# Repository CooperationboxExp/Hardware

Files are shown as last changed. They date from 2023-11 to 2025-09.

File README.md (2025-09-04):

# Hardware

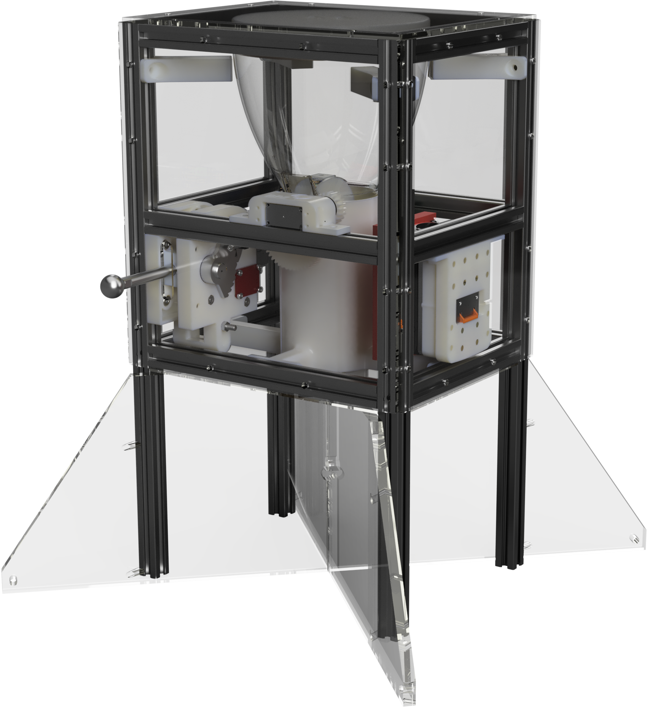
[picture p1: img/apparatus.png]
apparatus


## Publication

Repository: Zenodo  
Publication date: 2024-11-18  



## Electrical wireing

apparatus

## Manufacturing

The files for manufacturing can be found in the following folders:

+ STL/: Contains the STL files for 3D printing the parts.
+ Panels/: Contains the files for cutting the panels.
+ PDF/: Contains the files with specifications, turning and assembly instructions.

Alternatively, you can export all parts from the provided full assemblies with either the `ApparatusAssembly.step` or `ApparatusAssembly.f3z` files.

## BOM

From `BOM.xlsx`:

| Category | Quantity  One apparatus | Quantity four apparatuses | Wear and tear | Amount to order | Type / Length mm | Component | Supplier | URL | Price @ URL | Price for one apparatus. | Price for two apparatus. | Price waer and tear | Price total | Comment |
| --- | --- | --- | --- | --- | --- | --- | --- | --- | --- | --- | --- | --- | --- | --- |
| Housing | 100 | 400 | 0 | 400 | M5 | Nutenstein mit Steg I-Typ Nut 5 [M5] | Motedis | https://www.motedis.com/shop/Nutprofil-Zubehoer/Zubehoer-20-I-Typ-Nut-5/Nutensteine-passend-fuer-Nut-5-I-Typ/Nutenstein-mit-Steg-I-Typ-Nut-5-M5::4226.html | 0,18 € | 18,16 € | 72,64 € | 0,00 € | 72,64 € | |
| Housing | 4 | 16 | 0 | 16 | 500mm | Aluprofil 20x20 I-Typ Nut 5 | Motedis | https://www.motedis.com/shop/Aluprofile/20-I-Typ-Nut-5/Aluprofil-20x20-I-Typ-Nut-5::1076.html | 2,96 € | 11,82 € | 47,28 € | 0,00 € | 47,28 € | |
| Housing | 8 | 32 | 2 | 34 | 180mm, machining M5 L/R | Aluprofil 20x20 I-Typ Nut 5 | Motedis | https://www.motedis.com/shop/Aluprofile/20-I-Typ-Nut-5/Aluprofil-20x20-I-Typ-Nut-5::1076.html | 2,90 € | 23,20 € | 92,80 € | 5,80 € | 98,60 € | |
| Housing | 8 | 32 | 2 | 34 | 240mm, machining M5 L/R | Aluprofil 20x20 I-Typ Nut 5 | Motedis | https://www.motedis.com/shop/Aluprofile/20-I-Typ-Nut-5/Aluprofil-20x20-I-Typ-Nut-5::1076.html | 3,17 € | 25,32 € | 101,28 € | 6,33 € | 107,61 € | |
| Housing | 16 | 64 | 4 | 68 | 20x20 mm | Stahlwinkel 20 verzinkt | Motedis | https://www.motedis.com/shop/Test2-Systematic/Gabelkoepfe-Gabelgelenke/Stahlwinkel-20-verzinkt::9014.html | 0,72 € | 11,52 € | 46,08 € | 2,88 € | 48,96 € | |
| Housing | 56 | 224 | 15 | 239 | M5x6 | Schraube DIN EN ISO 7380 - Linsenkopfschraube | Motedis | https://www.motedis.com/shop/Mechanik-Basiselemente/DIN-Schrauben/Schraube-DIN-EN-ISO-7380-Linsenkopfschraube::1070.html | 0,15 € | 8,42 € | 33,69 € | 2,26 € | 35,95 € | |
| Housing | 56 | 224 | 15 | 239 | M5x8 | Schraube DIN EN ISO 7380 - Linsenkopfschraube | Motedis | https://www.motedis.com/shop/Mechanik-Basiselemente/DIN-Schrauben/Schraube-DIN-EN-ISO-7380-Linsenkopfschraube::1070.html | 0,15 € | 8,42 € | 33,69 € | 2,26 € | 35,95 € | |
| Housing | 56 | 224 | 15 | 239 | M5x10 | Schraube DIN EN ISO 7380 - Linsenkopfschraube | Motedis | https://www.motedis.com/shop/Mechanik-Basiselemente/DIN-Schrauben/Schraube-DIN-EN-ISO-7380-Linsenkopfschraube::1070.html | 0,15 € | 8,42 € | 33,69 € | 2,26 € | 35,95 € | |
| Housing | 56 | 224 | 15 | 239 | M5x12 | Schraube DIN EN ISO 7380 - Linsenkopfschraube | Motedis | https://www.motedis.com/shop/Mechanik-Basiselemente/DIN-Schrauben/Schraube-DIN-EN-ISO-7380-Linsenkopfschraube::1070.html | 0,15 € | 8,42 € | 33,69 € | 2,26 € | 35,95 € | |
| Housing | 0 | 0 | 0 | 0 | M5x12 | Befestigungsschraube DIN 7380 M5x12 vz für Standardverbinder Nut 5 I-Typ | Motedis | https://www.motedis.com/shop/Nutprofil-Zubehoer/Zubehoer-20-I-Typ-Nut-5/Verbinder-Winkel/Befestigungsschraube-DIN-7380-M5x12-vz-f%FCr-Standardverbinder-Nut-5-I-Typ::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 | 0,11 € | 0,00 € | 0,00 € | 0,00 € | 0,00 € | |
| Housing | 20 | 80 | 15 | 95 | M5x16 | Schraube DIN EN ISO 7380 - Linsenkopfschraube | Motedis | https://www.motedis.com/shop/Mechanik-Basiselemente/DIN-Schrauben/Schraube-DIN-EN-ISO-7380-Linsenkopfschraube::1070.html | 0,15 € | 3,01 € | 12,03 € | 2,26 € | 14,29 € | |
| Housing | 0 | 0 | 0 | 0 | 35x220mm | DIN 35 – Hutschiene | Digikey | https://www.digikey.de/product-detail/de/banner-engineering-corporation/DIN-35-220/2170-DIN-35-220-ND/12417670 | 18,25 € | 0,00 € | 0,00 € | 0,00 € | 0,00 € | |
| Housing | 10 | 40 | 15 | 55 | M5x35 | Schraube DIN EN ISO 7380 - Linsenkopfschraube | Motedis | https://www.motedis.com/shop/Mechanik-Basiselemente/DIN-Schrauben/Schraube-DIN-EN-ISO-7380-Linsenkopfschraube::1070.html | 0,39 € | 3,90 € | 15,58 € | 5,84 € | 21,43 € | |
| | | | | | | | | | | | | | | |
| Food Dispenser | 1 | 3 | 0 | 3 | 320x220x3 | Cereal Dispenser | Amazon | https://www.amazon.de/-/en/United-Entertainment-Dispenser-Cornflakes-Cereals/dp/B06XQLSSG6?psc=1 | 29,00 € | 29,00 € | 87,00 € | 0,00 € | 87,00 € | |
| Food Dispenser | 1 | 4 | 0 | 4 | 320x220x3 | Cereal Dispenser | Kaufland | https://www.kaufland.de/product/358105876/?vid=347560386 | 19,90 € | 19,90 € | 79,60 € | 0,00 € | 79,60 € | |
| Food Dispenser | 1 | 4 | 4 | 8 | 900-00008 | Servo Continuous | Digikey | https://www.digikey.de/product-detail/de/parallax-inc/900-00008/900-00008-ND/1774454 | 10,95 € | 10,95 € | 43,80 € | 43,80 € | 87,60 € | |
| | | | | | | | | | | | | | | |
| Lever and lock | 2 | 8 | 4 | 12 | ROB-11965 | Servo 180° | Digikey | https://www.digikey.de/product-detail/en/sparkfun-electronics/ROB-11965/1568-1319-ND/5766906 | 10,95 € | 21,90 € | 87,60 € | 43,80 € | 131,40 € | |
| Lever and lock | 2 | 8 | 1 | 9 | Gleitlager | Igus Gleitlager mit Bund GFM-1618-09 | Motedis | https://www.motedis.com/shop/Dynamik-Basiselemente/Gleitlager/Igus-Gleitlager-mit-Bund-GFM-1618-09::5078.html | 2,44 € | 4,89 € | 19,54 € | 2,44 € | 21,99 € | |
| Lever and lock | 1 | 4 | 0 | 4 | CNC | Lever metal assembly | Internal workshop | | 0,00 € | 0,00 € | 0,00 € | 0,00 € | 0,00 € | |
| Lever and lock | 2 | 8 | 1 | 9 | AD 4, ID 3.54, Hf 16, H1 8.86 4.57 | Druckfeder C105 | Misumi | https://de.misumi-ec.com/vona2/detail/221000016945/?HissuCode=C105&PNSearch=C105 | 0,60 € | 1,20 € | 4,80 € | 0,60 € | 5,40 € | |
| Lever and lock | 1 | 1 | 0 | 1 | | 10279 Zugfeder Inhalt 350 Teile | Conrad | https://www.conrad.de/de/p/10279-zugfeder-inhalt-350-teile-887655.html?refresh=true | 138,65 € | 138,65 € | 138,65 € | 0,00 € | 138,65 € | We ended up using Z 104 41,4x6x0,55 mm |
| Lever and lock | 4 | 16 | 1 | 17 | M5x45 | Zylinderschraube mit Innensechskant nach DIN 912 | Misumi | https://de.misumi-ec.com/vona2/detail/221006347487/?HissuCode=912A2545 | 0,75 € | 3,00 € | 12,00 € | 0,75 € | 12,75 € | |
| Lever and lock | 6 | 24 | 8 | 32 | M5 | Mutter DIN 934 | Motedis | https://www.motedis.com/shop/Mechanik-Basiselemente/Basic-Basics/DIN-Normteile/DIN-Mutter/Mutter-DIN-934::1768.html | 0,29 € | 1,77 € | 7,08 € | 2,36 € | 9,43 € | |
| Lever and lock | 3 | 12 | 0 | 12 | M5x16 | Senkschraube mit Innensechskant nach DIN 7991 | Motedis | https://www.motedis.com/shop/Mechanik-Basiselemente/DIN-Schrauben/Senkschraube-mit-Innensechskant-nach-DIN-7991::1120.html | 0,39 € | 1,17 € | 4,68 € | 0,00 € | 4,68 € | |
| Lever and lock | 1 | 4 | 0 | 4 | M3 | Gewindestange >60mm | Conrad | https://www.conrad.de/de/p/reely-10589-gewindestange-m3-500-mm-stahl-1-st-237094.html | 1,42 € | 1,42 € | 5,68 € | 0,00 € | 5,68 € | |
| Lever and lock | 1 | 4 | 0 | 4 | M5 | Gewindestange >60mm | Conrad | https://www.conrad.de/de/p/reely-10591-m5-gewindestange-m5-500-mm-stahl-1-st-237116.html | 1,92 € | 1,92 € | 7,68 € | 0,00 € | 7,68 € | |
| Lever and lock | 2 | 8 | 2 | 10 | Microswitch | Omron Electronics Inc-EMC Div D2F-5L | Digikey | https://www.digikey.de/product-detail/de/omron-electronics-inc-emc-div/D2F-5L/Z8846-ND/8593137 | 3,19 € | 6,38 € | 25,52 € | 6,38 € | 31,90 € | |
| | | | | | | | | | | | | | | |
| Panels | 1 | 4 | 0 | 4 | 4mm (32,00 €/m²), 1500x700mm | MAKROLON, POLYCARBONAT | Ebay | https://www.ebay.de/itm/263920803844 | 57,75 € | 57,75 € | 231,00 € | 0,00 € | 231,00 € | Alternative to internal workshop |
| Panels | 1 | 4 | 0 | 4 | 10mm (32,00 €/m²), 1500x700mm | MAKROLON, POLYCARBONAT | Ebay | https://www.ebay.de/itm/263920803844 | 136,50 € | 136,50 € | 546,00 € | 0,00 € | 546,00 € | Alternative to internal workshop |
| Panels | 1 | 4 | 0 | 4 | 4mm (32,00 €/m²), 1500x700mm | MAKROLON, POLYCARBONAT | Internal workshop | | 0,00 € | 0,00 € | 0,00 € | 0,00 € | 0,00 € | |
| Panels | 1 | 4 | 0 | 4 | 10mm (32,00 €/m²), 1500x700mm | MAKROLON, POLYCARBONAT | Internal workshop | | 0,00 € | 0,00 € | 0,00 € | 0,00 € | 0,00 € | |
| Panels | 1 | 4 | 0 | 4 | Top.dxf | 4mm Polycarbonat clear | kunststoffplattenonline.de | https://kunststoffplattenonline.de/product/polycarbonat-platten-transparent-klar-4-mm/ | 13,48 € | 13,48 € | 53,92 € | 0,00 € | 53,92 € | Alternative to internal workshop |
| Panels | 2 | 8 | 0 | 8 | Sides.dxf | 4mm Polycarbonat clear | kunststoffplattenonline.de | https://kunststoffplattenonline.de | 14,67 € | 29,34 € | 117,36 € | 0,00 € | 117,36 € | Alternative to internal workshop |
| Panels | 1 | 4 | 0 | 4 | Front.dxf | 4mm Polycarbonat clear | kunststoffplattenonline.de | https://kunststoffplattenonline.de | 17,81 € | 17,81 € | 71,24 € | 0,00 € | 71,24 € | Alternative to internal workshop |
| Panels | 1 | 4 | 0 | 4 | BackPlate.dxf | 4mm Polycarbonat clear | kunststoffplattenonline.de | https://kunststoffplattenonline.de | 16,91 € | 16,91 € | 67,64 € | 0,00 € | 67,64 € | Alternative to internal workshop |
| Panels | 1 | 4 | 0 | 4 | DividerA.dxf | 10mm Polycarbonat clear | kunststoffplattenonline.de | https://kunststoffplattenonline.de/product/polycarbonat-platten-transparent-klar-10-mm/ | 54,17 € | 54,17 € | 216,68 € | 0,00 € | 216,68 € | Alternative to internal workshop |
| Panels | 1 | 4 | 0 | 4 | DividerB.dxf | 10mm Polycarbonat clear | kunststoffplattenonline.de | https://kunststoffplattenonline.de/product/polycarbonat-platten-transparent-klar-10-mm/ | 54,79 € | 54,79 € | 219,16 € | 0,00 € | 219,16 € | Alternative to internal workshop |
| | | | | | | | | | | | | | | |
| Miscellaneous | 5 | 20 | 0 | 20 | 3D Druck ABS+ | ESUN ABS+ 1,75mm nature | vonwange | https://vonwange.com/product/abs-175mm-nature/ | 18,99 € | 94,95 € | 379,80 € | 0,00 € | 379,80 € | |
| Miscellaneous | 1 | 1 | 0 | 1 | 3D Druck Gewindeeinsätze | ruthex Threaded Insert, Brass Threaded Bushings | Amazon | https://www.amazon.de/-/en/ruthex%C2%AE-threaded-Press-fit-plastic-ultrasound/dp/B08K1BVGN9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 | 29,99 € | 29,99 € | 29,99 € | 0,00 € | 29,99 € | |
| | | | | | | | | | | | | | | |
| Battery | 0 | 0 | 0 | 0 | | Bosch Charger | Amazon | https://www.amazon.de/-/en/Bosch-Professional-system-battery-5-0Ah/dp/B00IKI352E | 44,95 € | 0,00 € | 0,00 € | 0,00 € | 0,00 € | Alternative to Bosch Batterie Set |
| Battery | 1 | 4 | 0 | 4 | | Bosch Batterie | Amazon | https://www.amazon.de/-/en/Bosch-Professional-system-battery-5-0Ah/dp/B00IKI352E | 60,00 € | 60,00 € | 240,00 € | 0,00 € | 240,00 € | Alternative to Bosch Batterie Set |
| Battery | 2 | 2 | 0 | 2 | | Bosch Batterie Set | Conrad | https://www.conrad.de/de/p/bosch-professional-1600a01ba3-werkzeug-akku-und-ladegeraet-18-v-li-ion-2127378.html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 | 159,66 € | 319,32 € | 319,32 € | 0,00 € | 319,32 € | |
| Battery | 1 | 4 | 1 | 5 | modified as battery interface | Bosch Adapter | Amazon | https://www.amazon.de/-/en/Ladieshow-Battery-Adaptor-Convert-Converter/dp/B08QJK9DW4/261-3484322-5351609?psc=1 | 22,99 | 22,99 € | 91,96 € | 22,99 € | 114,95 € | |
| | | | | | | | | | | | | | | |
| Controller and electronics | 1 | 4 | 4 | 8 | Control unit expansion board | Whadda Erweiterungsmodul | Conrad | https://www.conrad.de/de/p/whadda-erweiterungsmodul-2481837.html | 9,24 € | 9,24 € | 36,96 € | 36,96 € | 73,92 € | |
| Controller and electronics | 2 | 8 | 4 | 12 | Voltage supply | Joy-it XL6019 Step-up Converter 1 St. | Conrad | https://www.conrad.de/de/p/joy-it-xl6019-step-up-converter-1-st-1697651.html | 4,61 € | 9,22 € | 36,88 € | 18,44 € | 55,32 € | |
| Controller and electronics | 2 | 8 | 2 | 10 | Voltage supply | Pololu Adjustable 4-12V Step-Up Step-Down Spannungsregler S18V20ALV | Conrad | https://www.conrad.de/de/p/pololu-adjustable-4-12v-step-up-step-down-spannungsregler-s18v20alv-802236410.html | 49,54 € | 99,08 € | 396,32 € | 99,08 € | 495,40 € | |
| Controller and electronics | 1 | 4 | 1 | 5 | Control unit | Arduino Board Nano Core, Nano ATMega328 | Conrad | https://www.conrad.de/de/p/arduino-board-nano-core-nano-atmega328-1172623.html | 21,00 € | 21,00 € | 84,00 € | 21,00 € | 105,00 € | |
| Controller and electronics | 1 | 4 | 1 | 5 | Remote control | H-Tronic HT1S Funksender 1-Kanal Frequenz 868.35 MHz 3 V Reichweite max. (im Freifeld) 150 m | Conrad | https://www.conrad.de/de/p/h-tronic-ht1s-funksender-1-kanal-frequenz-868-35-mhz-3-v-reichweite-max-im-freifeld-150-m-1597514.html | 22,68 € | 22,68 € | 90,72 € | 22,68 € | 113,40 € | |
| Controller and electronics | 1 | 4 | 1 | 5 | Remote receiver | H-Tronic HT1E Funkempfänger 1-Kanal Frequenz 868.35 MHz 12 V/DC | Conrad | https://www.conrad.de/de/p/h-tronic-ht1e-funkempfaenger-1-kanal-frequenz-868-35-mhz-12-v-dc-1406364.html | 37,81 € | 37,81 € | 151,24 € | 37,81 € | 189,05 € | |
| Controller and electronics | 1 | 4 | 1 | 5 | Arduino transceiver | WRL-00691 - SPARKFUN TRANSCEIVER BREAKOUT BOARD | Digikey | https://www.digikey.de/de/products/detail/sparkfun-electronics/WRL-00691/5762445 | 21,15 € | 21,15 € | 84,60 € | 21,15 € | 105,75 € | |
| Controller and electronics | 1 | 1 | 0 | 1 | Cabels Battery | eg. Litze 2.5 mm^2 | | | | 0,00 € | 0,00 € | 0,00 € | 0,00 € | Workshop supplies |
| Controller and electronics | 1 | 1 | 0 | 1 | Cabels | eg. Litze 0.25 mm^2 | | | | 0,00 € | 0,00 € | 0,00 € | 0,00 € | Workshop supplies |
| Controller and electronics | 1 | 1 | 0 | 1 | Dupont Connector 2.54mm Pitch | For "pin-header" | | | | 0,00 € | 0,00 € | 0,00 € | 0,00 € | Workshop supplies |
| Controller and electronics | 1 | 1 | 0 | 1 | WAGO Sortiment | | Conrad | https://www.conrad.de/de/p/wago-wa-741-644-verbindungsklemmen-sortiment-flexibel-0-14-4-mm-starr-0-2-4-mm-105-st-1398220.html | 52,09 € | 52,09 € | 52,09 € | 0,00 € | 52,09 € | Workshop supplies |
| Controller and electronics | 1 | 1 | 0 | 1 | Cabels | | | | | 0,00 € | 0,00 € | 0,00 € | 0,00 € | Workshop supplies |
| | | | | | | | | | | | | | | |

## Included CAD

For convenience some files included in this design where imported from external sources.

| Name | Author | Link |
| --- | --- | --- |
| Arduino Nano R3 ATmega 328P | MRMS - WORKSHOP | <https://grabcad.com/library/arduino-nano-r3-atmega-328p-1> |
| DFR0012 pour Arduino Nano | RedOhm | <https://grabcad.com/library/dfr0012-pour-arduino-nano-1> |
| Дрели - шуруповёрт / Drills - screwdriver | Alex Petuhov | <https://grabcad.com/library/drills-screwdriver-1> |
| Battery adapter | bujh bdfyjd | <https://grabcad.com/library/battery-adapter-1> |
| Servo | Amazon Seller | An Amazon page of a similar product that is unfortunately no longer available |

### GrabCAD terms

[https://grabcad.com/terms](https://grabcad.com/terms)

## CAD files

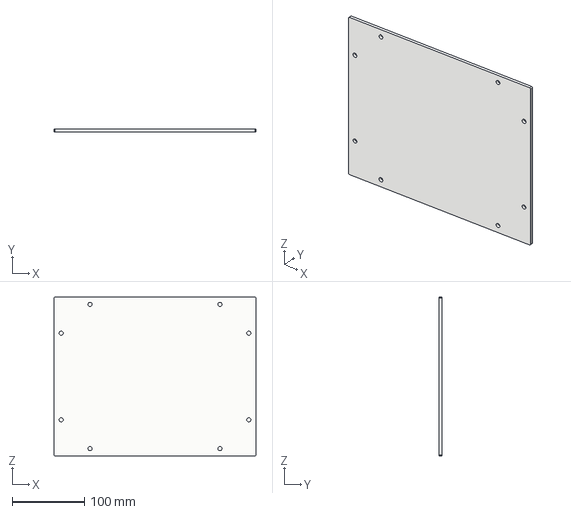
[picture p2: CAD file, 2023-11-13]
Panels/Top.step
280.0 x 4.00 x 220.0 mm

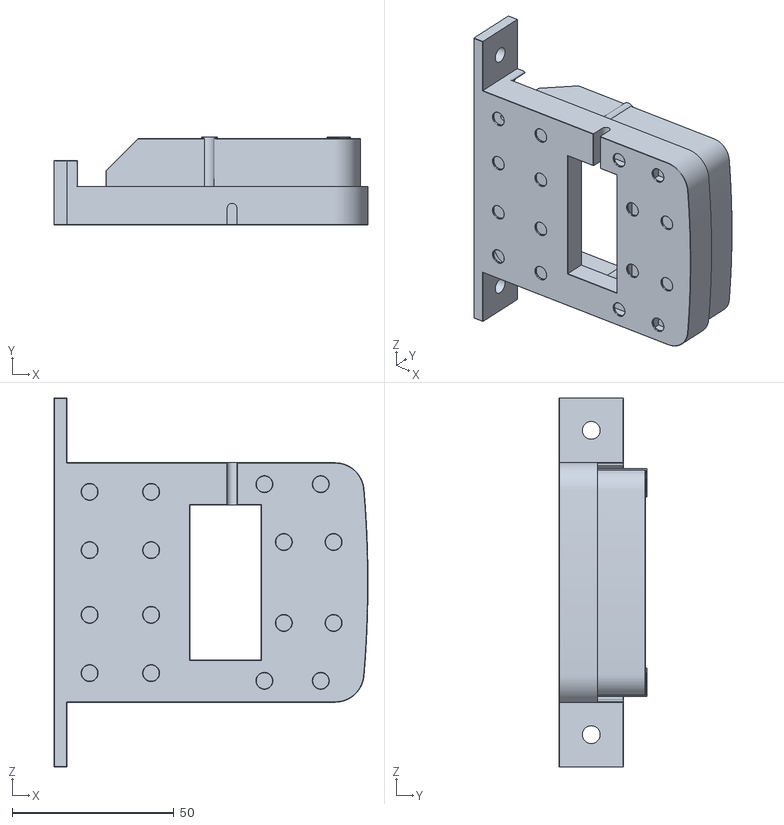
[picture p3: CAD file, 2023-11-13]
STL/BatterySocket_Interface v7.stl
97.0 x 27.2 x 114.0

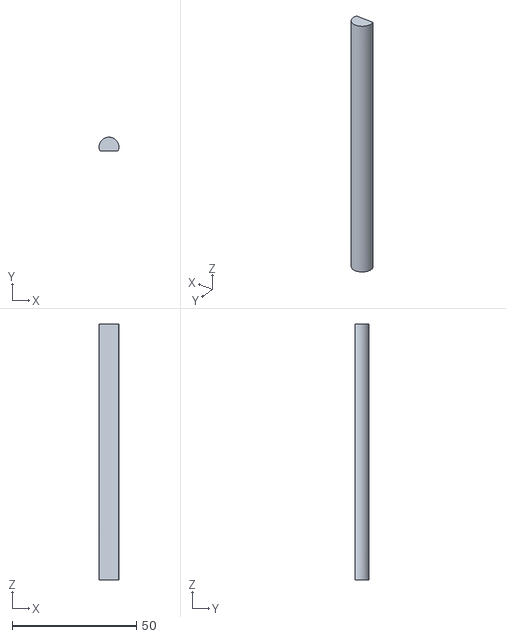
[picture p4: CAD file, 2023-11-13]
STL/Container/Axis.stl
8.00 x 5.50 x 103.0

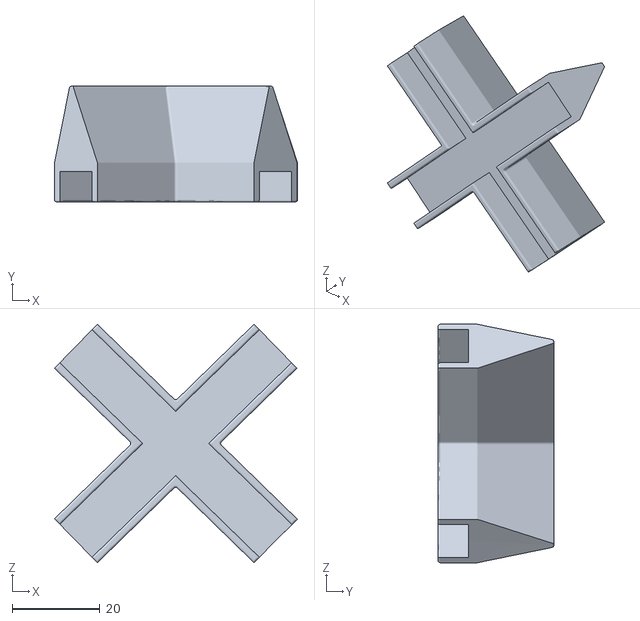
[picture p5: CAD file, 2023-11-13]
STL/Divider/FourSide_DividerModule.stl
55.4 x 26.5 x 54.4

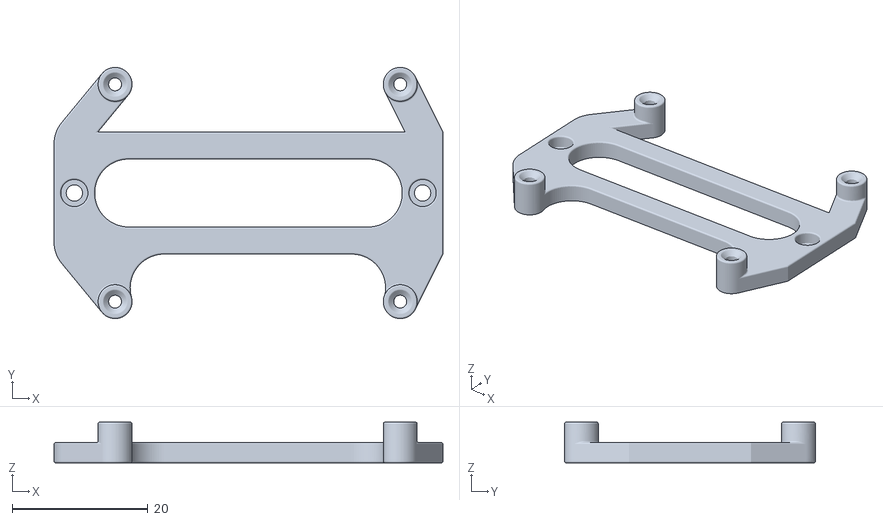
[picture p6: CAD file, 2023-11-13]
STL/Electronics/HT1E_Bracket.stl
57.3 x 37.0 x 6.00

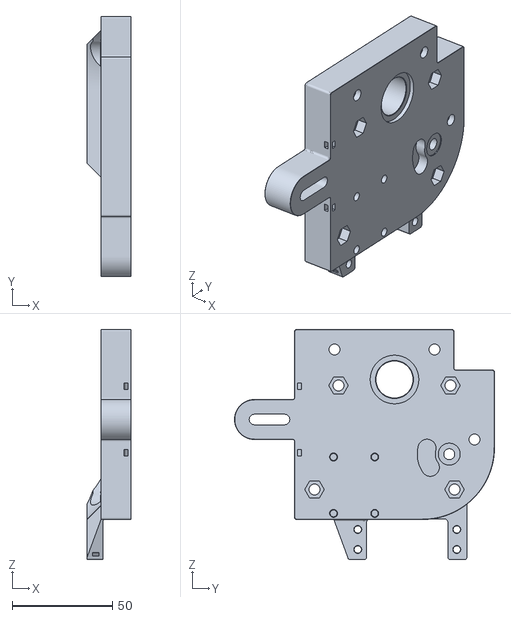
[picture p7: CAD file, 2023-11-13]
STL/Hebel_Assembly v4/Hebel_Plate_R.stl
22.0 x 130.0 x 115.0

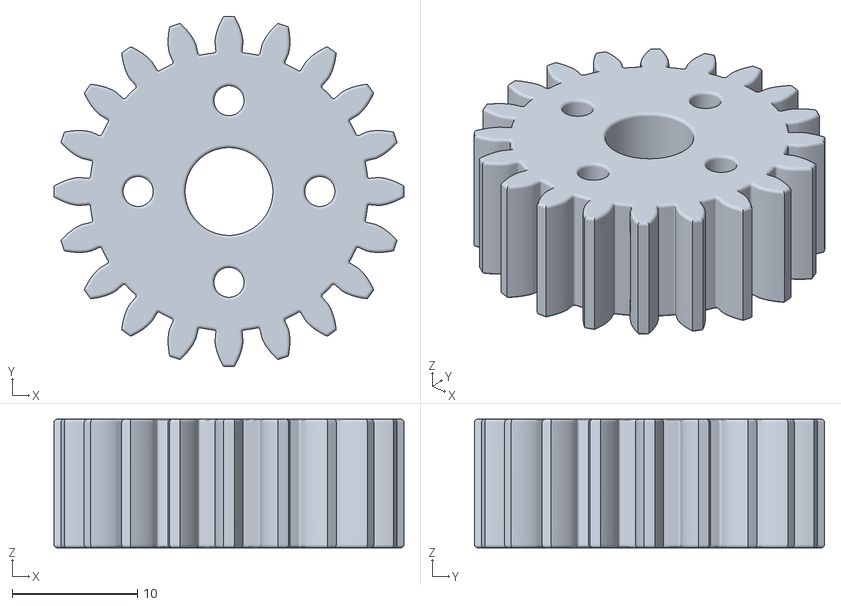
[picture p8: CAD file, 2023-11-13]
STL/ServoGear/GearCore.stl
27.9 x 27.9 x 10.3

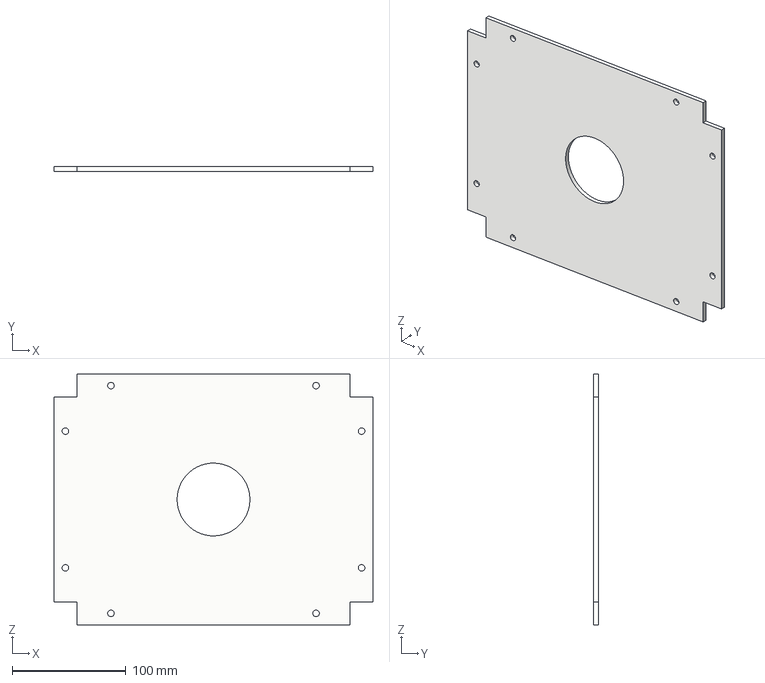
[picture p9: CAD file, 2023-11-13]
Panels/Bottom.step
280.0 x 4.00 x 220.0 mm

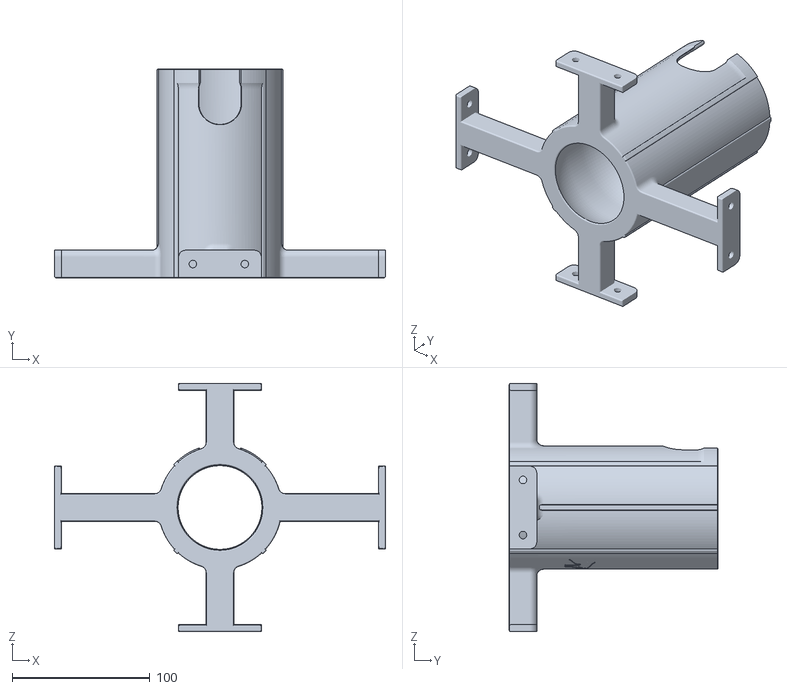
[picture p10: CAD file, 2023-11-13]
STL/Container/LowerContainerHolder.stl
240.0 x 151.3 x 180.0

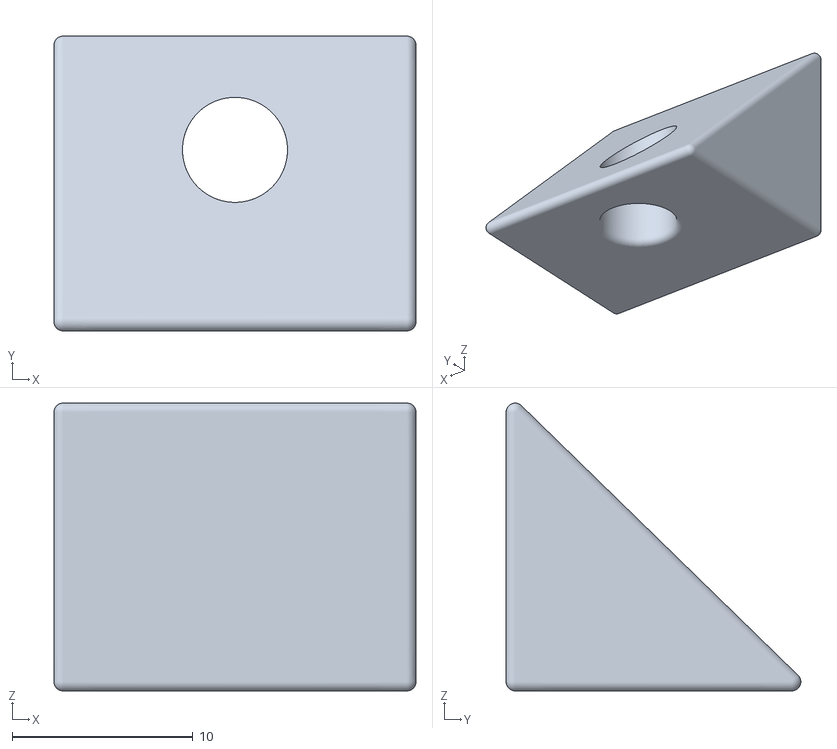
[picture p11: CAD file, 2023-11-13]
STL/Divider/SpacerA.stl
20.0 x 16.3 x 15.9

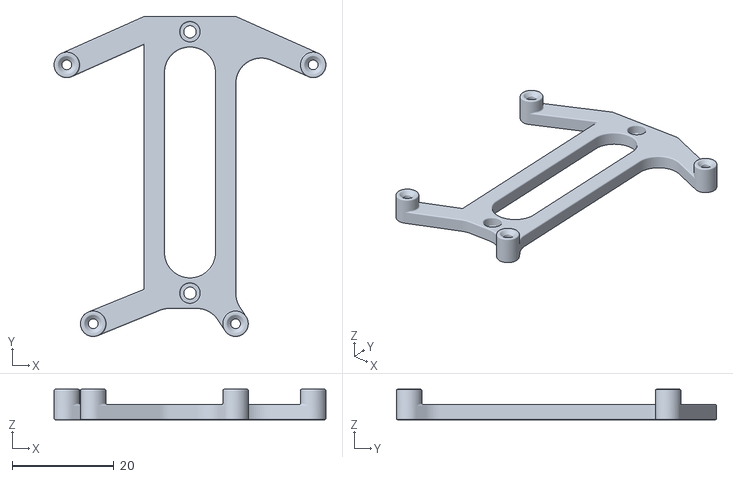
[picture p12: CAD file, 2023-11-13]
STL/Electronics/WPB210_Bracket.stl
53.4 x 62.8 x 6.00

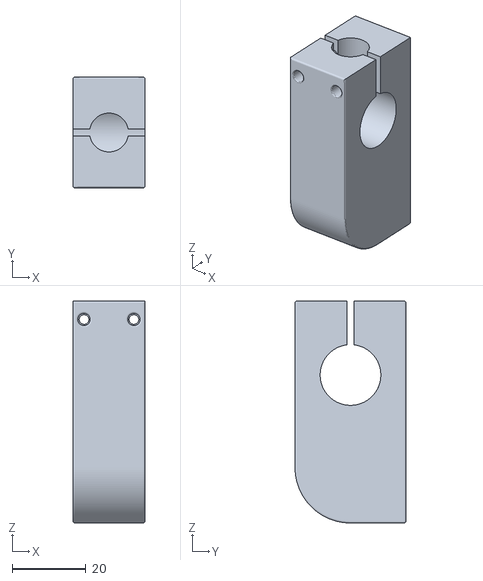
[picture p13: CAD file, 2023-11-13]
STL/Hebel_Assembly v4/Lever_Connector.stl
19.5 x 30.0 x 60.0

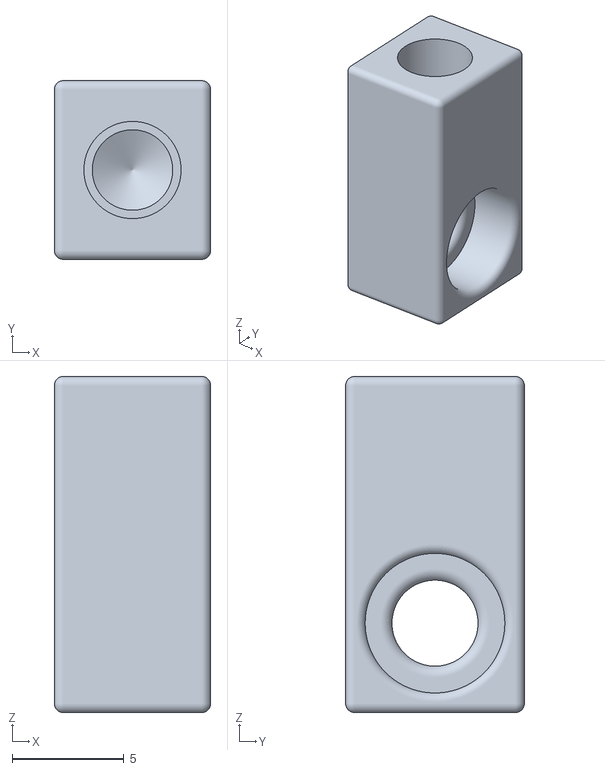
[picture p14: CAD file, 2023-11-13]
STL/Hebel_Assembly v4/SpringConnector/ServoConnector.stl
7.00 x 8.00 x 15.0

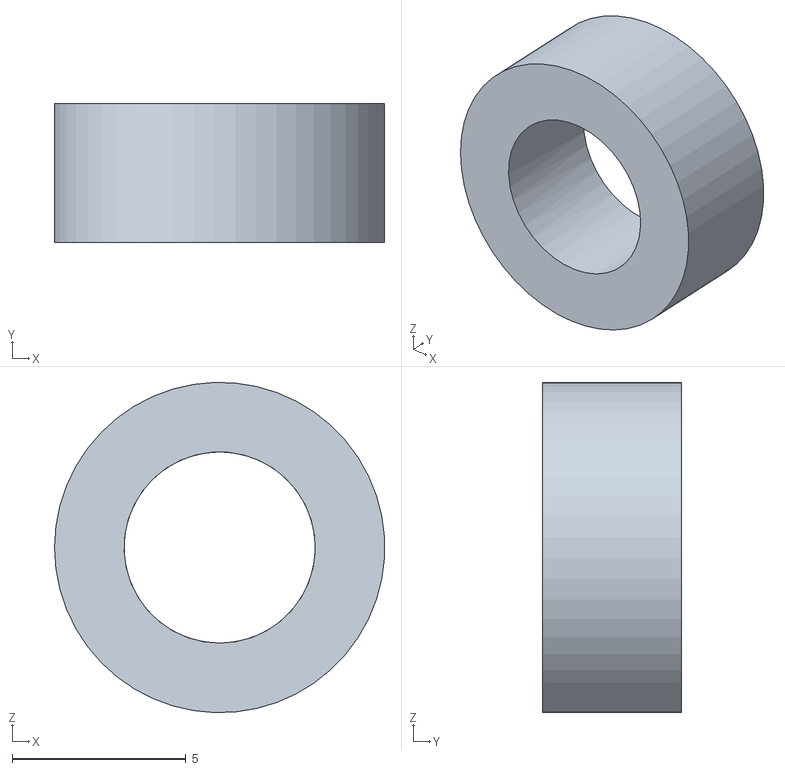
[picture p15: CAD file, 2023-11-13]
STL/PanelSpacer.stl
9.49 x 4.00 x 9.50

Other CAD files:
STL/ServoGear/ServoSlider.stl
Panels/Front.step
STL/Container/ContainerSpacer.stl
STL/Divider/OneSide_DividerModule.stl
Panels/BackPlate.dxf
Panels/BackPlate.step
Panels/Bottom.dxf
Panels/DividerA.dxf
Panels/DividerA.step
Panels/DividerB.dxf
Panels/DividerB.step
Panels/Front.dxf
Panels/Sides.dxf
Panels/Sides.step
Panels/Top.dxf
STL/Container/ContainerSpacer(Mirror).stl
STL/Divider/SpacerB.stl
STL/Electronics/2020_I-Type_Bracket.stl
STL/Electronics/DFR_Bracket.stl
STL/Electronics/S18V20ALV_Bracket.stl
STL/Hebel_Assembly v4/Axle.step
STL/Hebel_Assembly v4/Hebel_Plate_L(Mirror).stl
STL/Hebel_Assembly v4/Hebel_Plate_L.stl
STL/Hebel_Assembly v4/Hebel_Plate_R(Mirror).stl
STL/Hebel_Assembly v4/Klinke.step
STL/Hebel_Assembly v4/Lever.step
STL/Hebel_Assembly v4/MessingLager.step
STL/Hebel_Assembly v4/Passfeder.step
STL/Hebel_Assembly v4/Sperrad.step
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

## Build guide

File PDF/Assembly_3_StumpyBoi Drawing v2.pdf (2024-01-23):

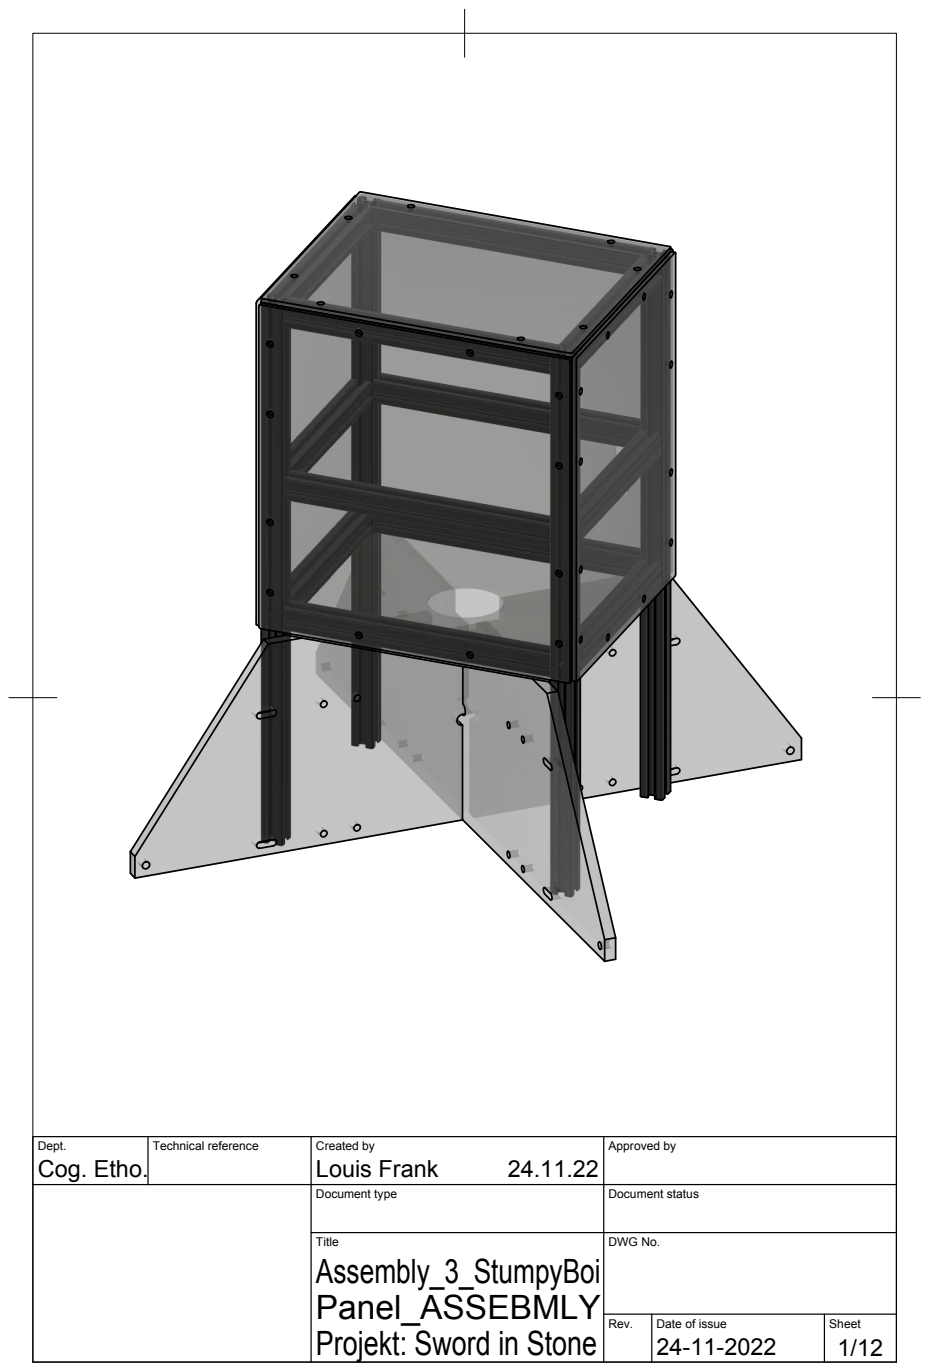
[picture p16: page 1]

Dept. Cog. Etho. | Technical reference | Created by Louis Frank 24.11.22 | Approved by

Document type | Document status

Title Assembly_3_StumpyBoi Panel_ASSEBMLY Projekt: Sword in Stone | DWG No.

Rev. | Date of issue 24-11-2022 | Sheet

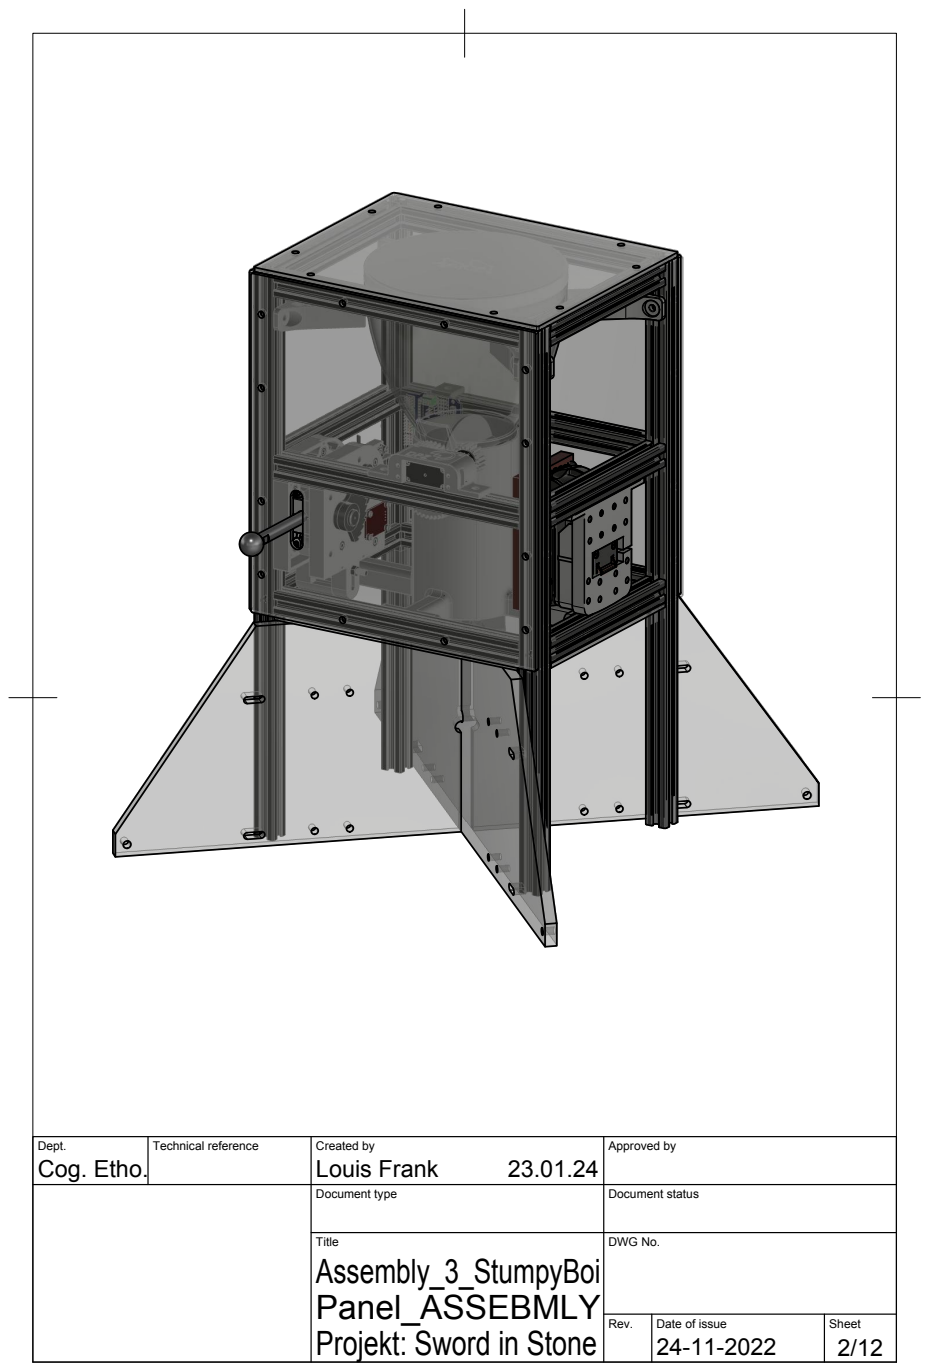
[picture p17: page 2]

Dept. Cog. Etho. | Technical reference | Created by Louis Frank 23.01.24 | Approved by

Document type | Document status

Title Assembly_3_StumpyBoi Panel_ASSEBMLY | DWG No.

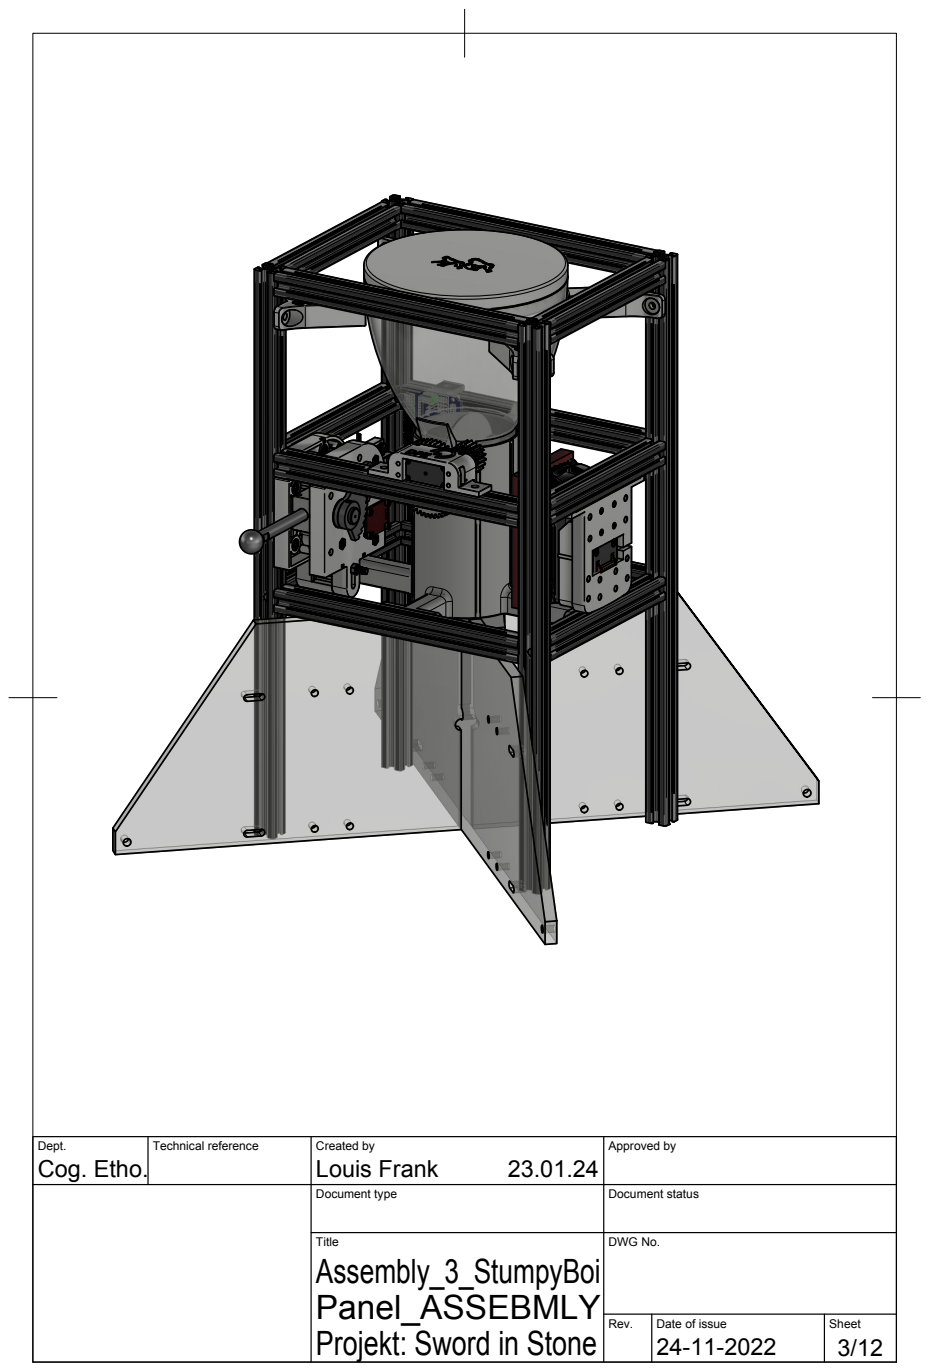
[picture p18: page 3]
Dept.; Technical reference; Created by; Approved by; Document type; Document status; Title; DWG No.; Cog. Etho.; Louis Frank

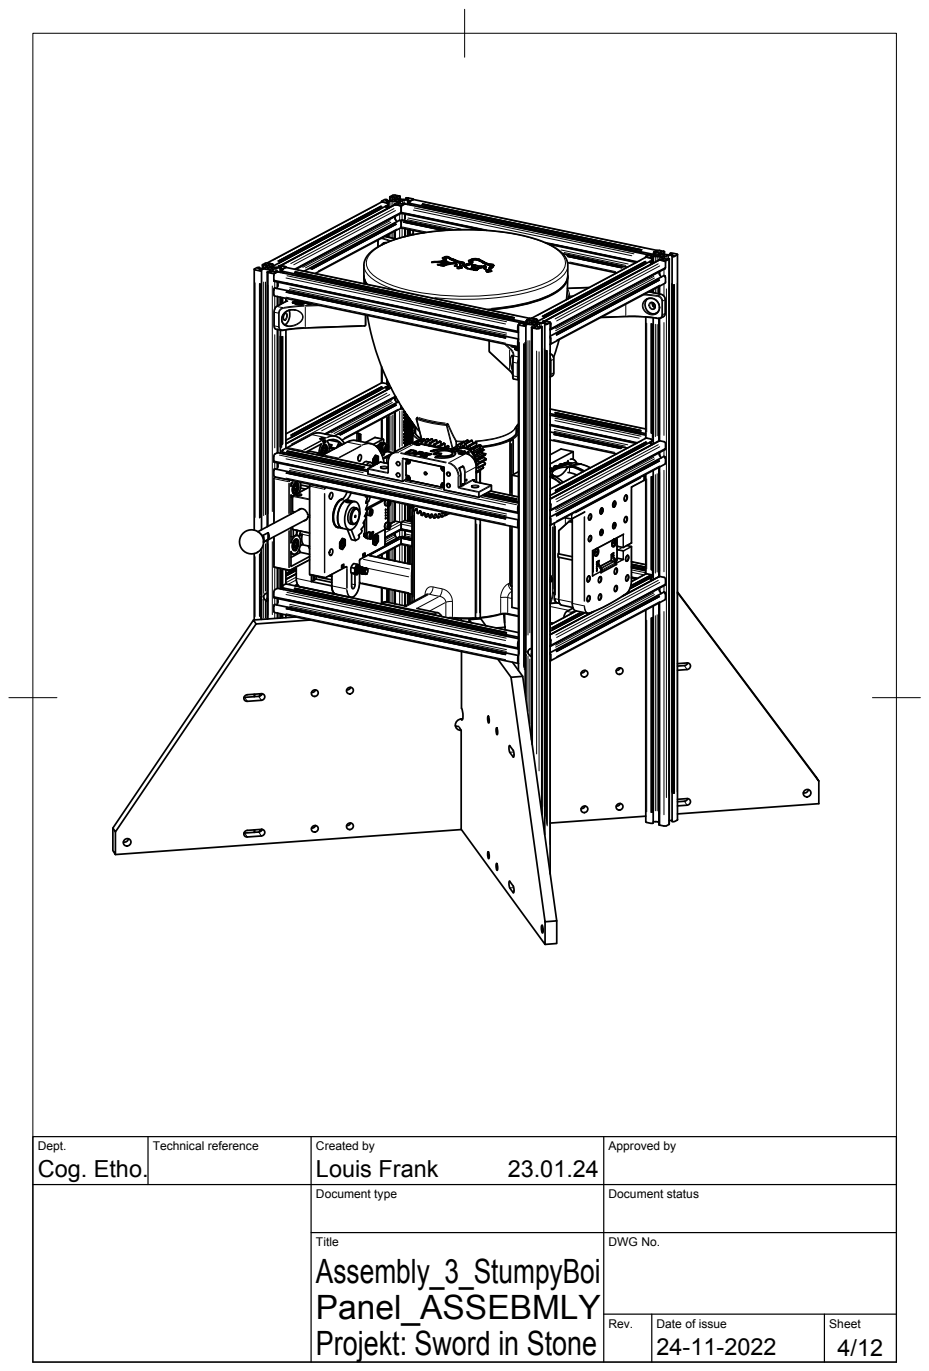
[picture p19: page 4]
Dept.; Technical reference; Created by; Approved by; Document type; Document status; Title; DWG No.; Cog. Etho.; Louis Frank

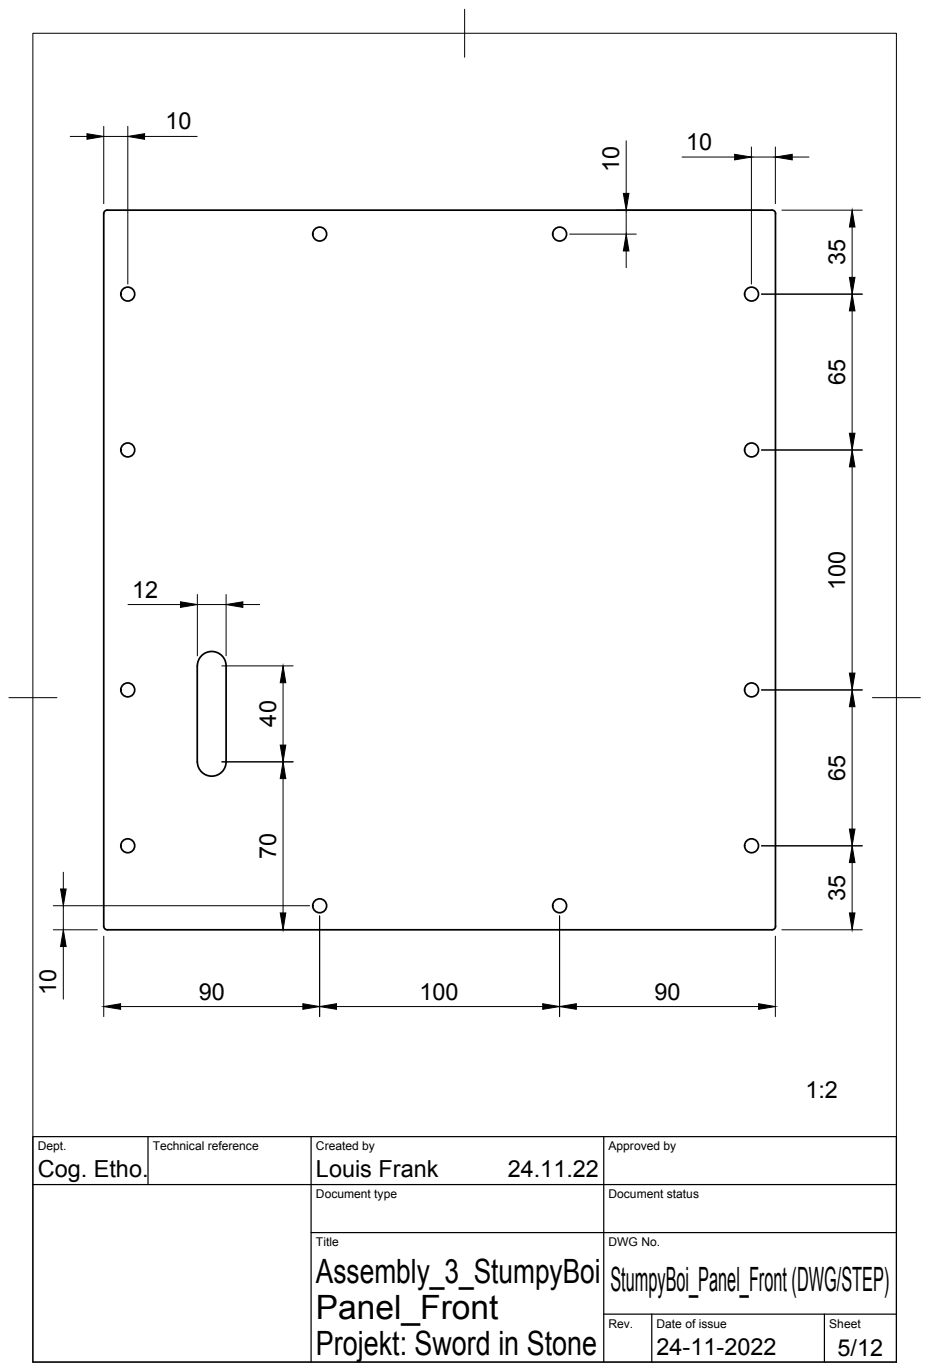
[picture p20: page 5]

Dept. Cog. Etho. | Technical reference | Created by Louis Frank 24.11.22 | Approved by

Document type | Document status

Title Assembly_3_StumpyBoi Panel_Front | DWG No. StumpyBoi_Panel_Front (DWG/STEP)

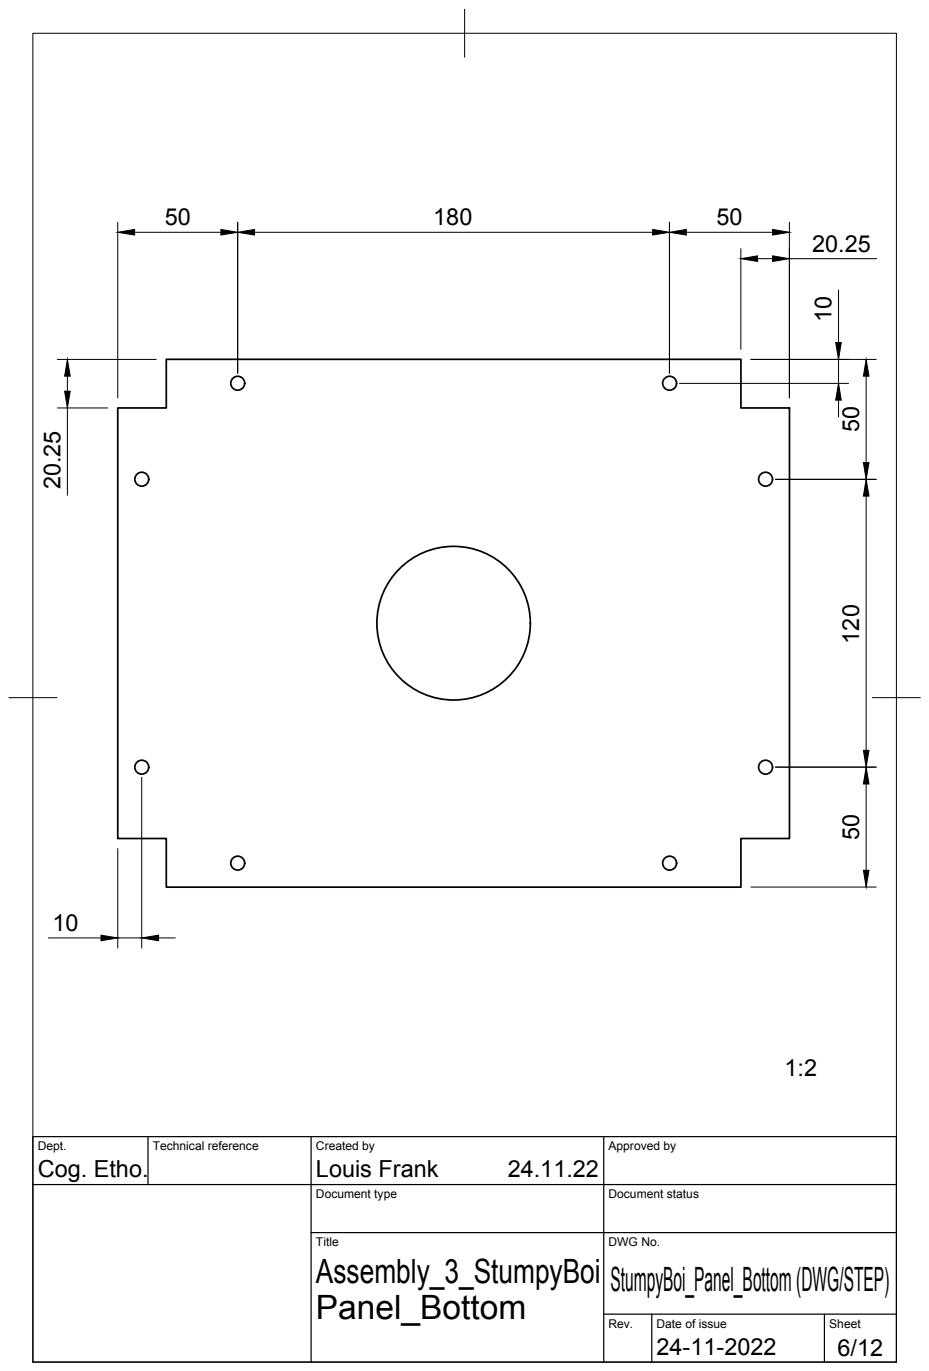
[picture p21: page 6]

Dept. Cog. Etho. | Technical reference | Created by Louis Frank 24.11.22 | Approved by

Document type | Document status

Title Assembly_3_StumpyBoi Panel_Bottom | DWG No. StumpyBoi_Panel_Bottom (DWG/STEP)

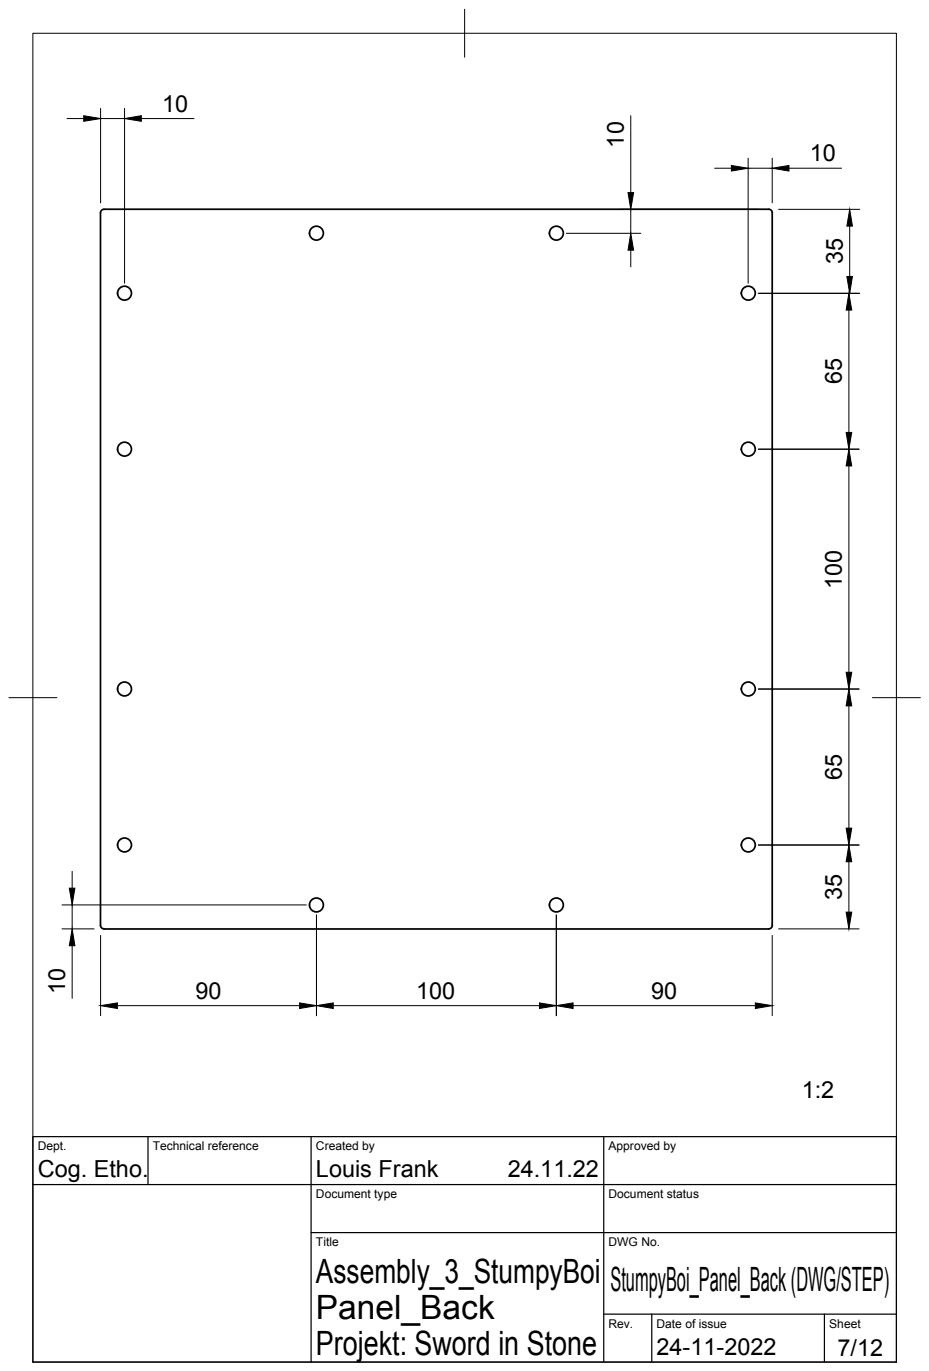
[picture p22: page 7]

Dept. Cog. Etho. | Technical reference | Created by Louis Frank 24.11.22 | Approved by

Document type | Document status

Title Assembly_3_StumpyBoi Panel_Back | DWG No. StumpyBoi_Panel_Back (DWG/STEP)

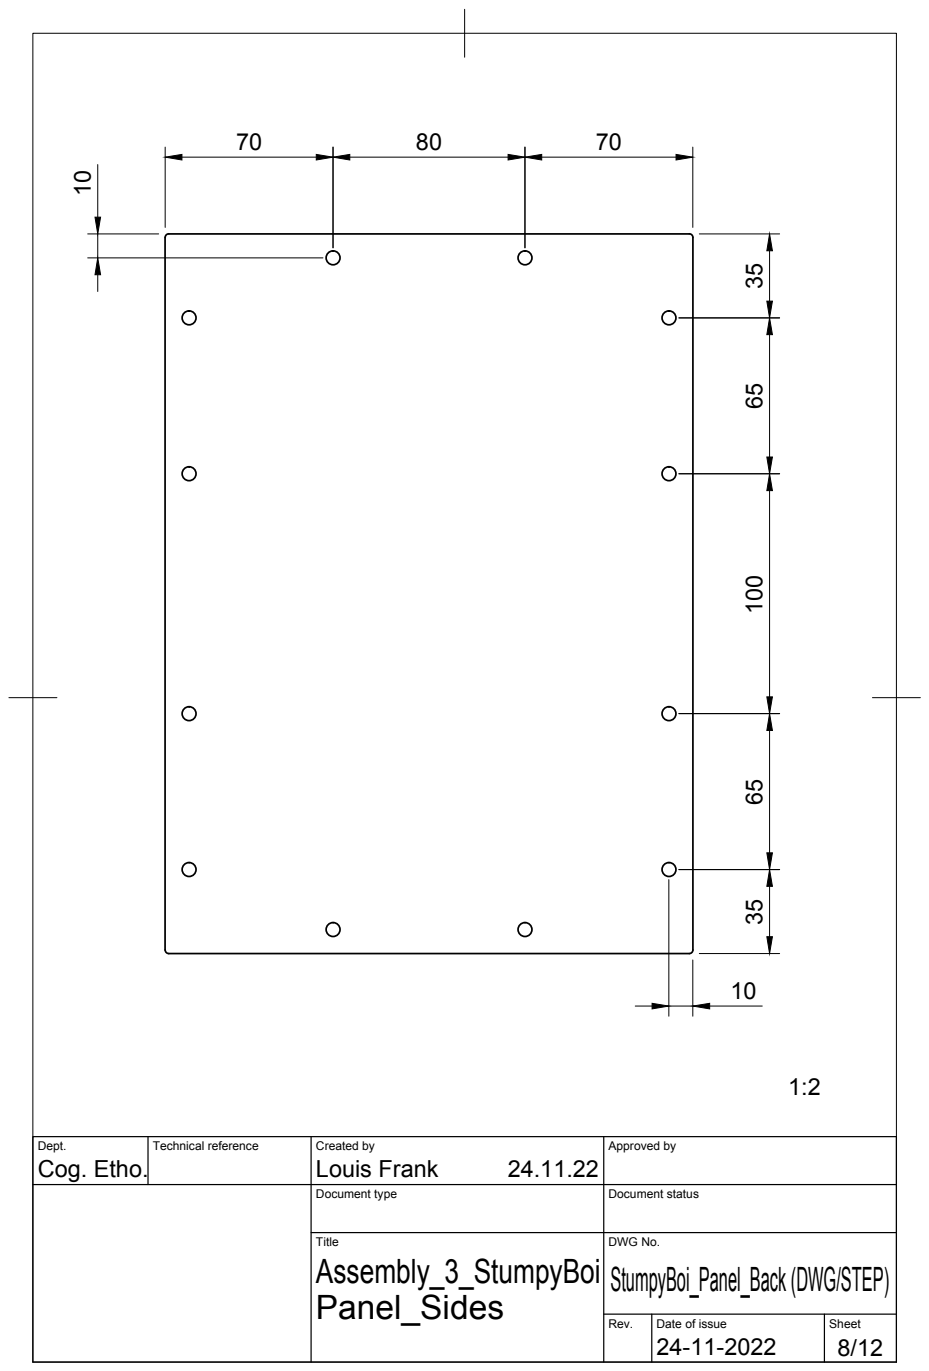
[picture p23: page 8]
Cog. Etho.; Louis Frank

Dept. | Technical reference | Created by 24.11.22 | Approved by

Document type | Document status

Title Assembly_3_StumpyBoi Panel_Sides | DWG No. StumpyBoi_Panel_Back (DWG/STEP)

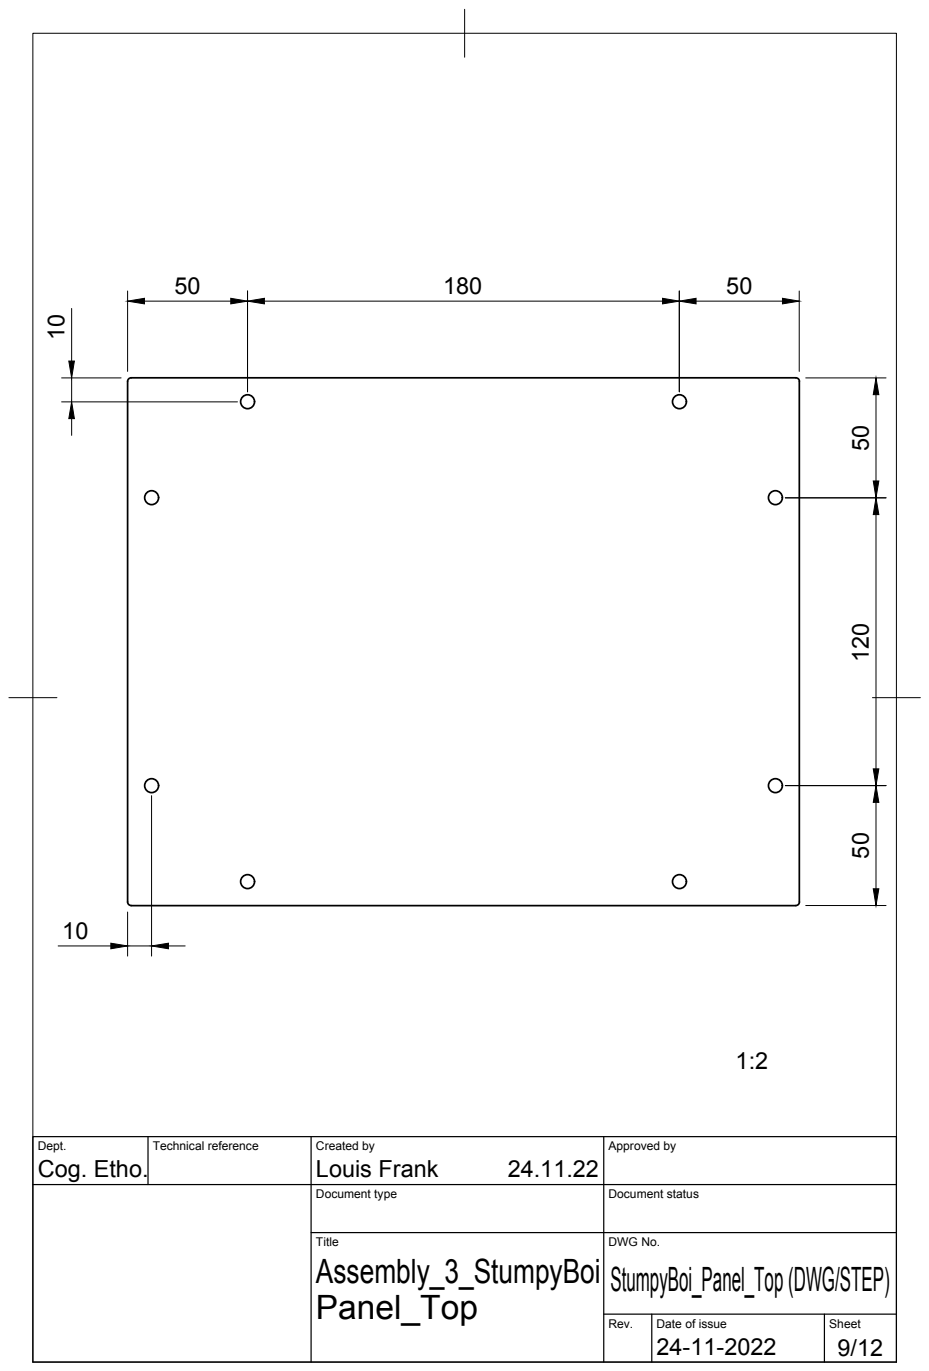
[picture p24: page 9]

Dept. Cog. Etho. | Technical reference | Created by Louis Frank 24.11.22 | Approved by

Document type | Document status

Title Assembly_3_StumpyBoi Panel_Top | DWG No. StumpyBoi_Panel_Top (DWG/STEP)

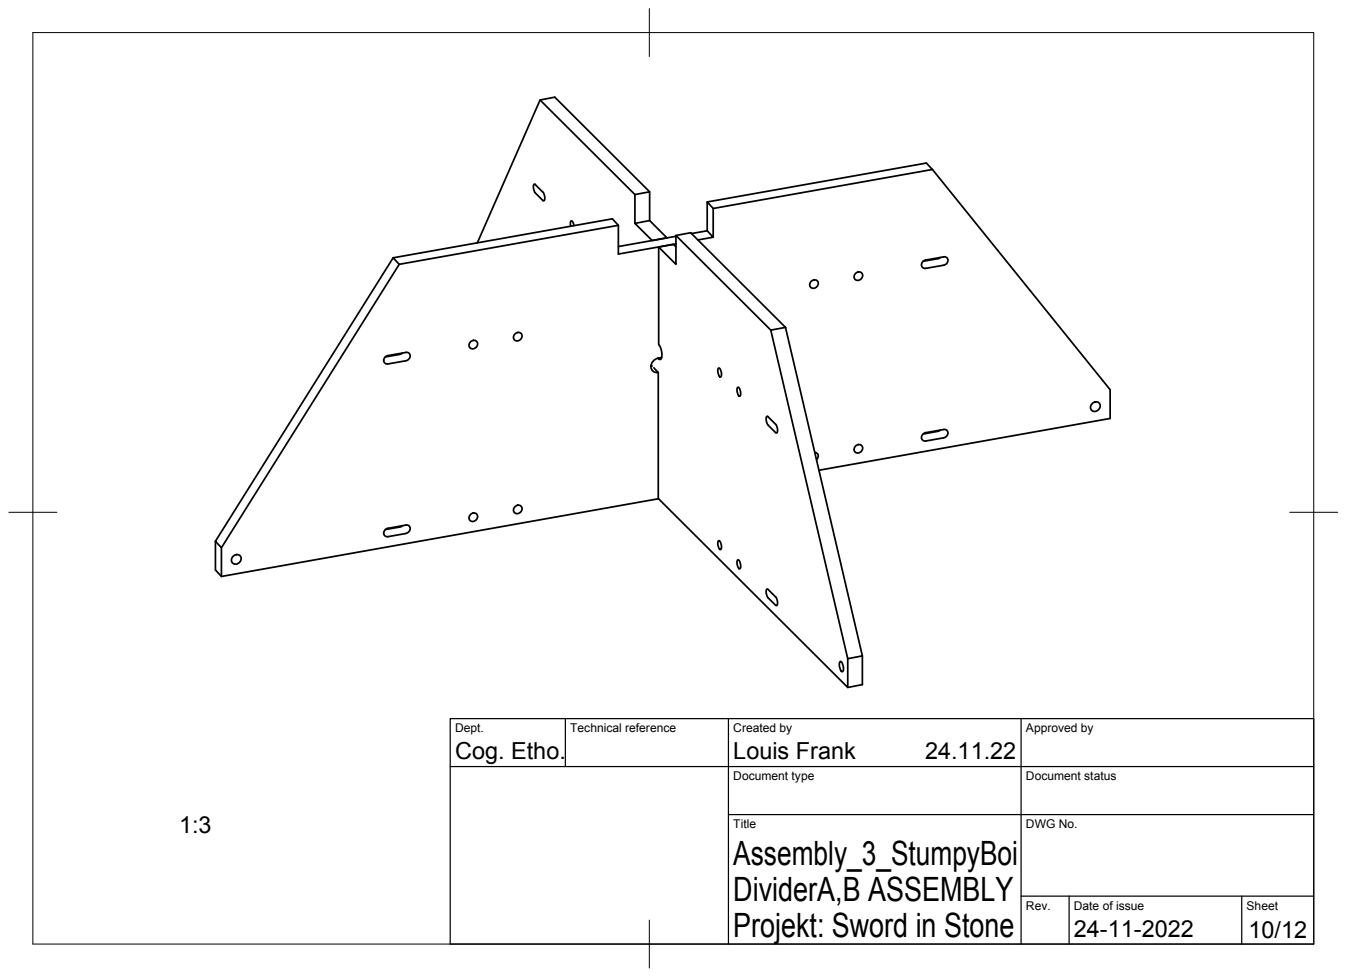
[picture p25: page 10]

Dept. Cog. Etho. | Technical reference | Created by Louis Frank 24.11.22 | Approved by

Document type | Document status

Title Assembly_3_StumpyBoi DividerA,B ASSEMBLY | DWG No.

Rev. | Date of issue | Sheet

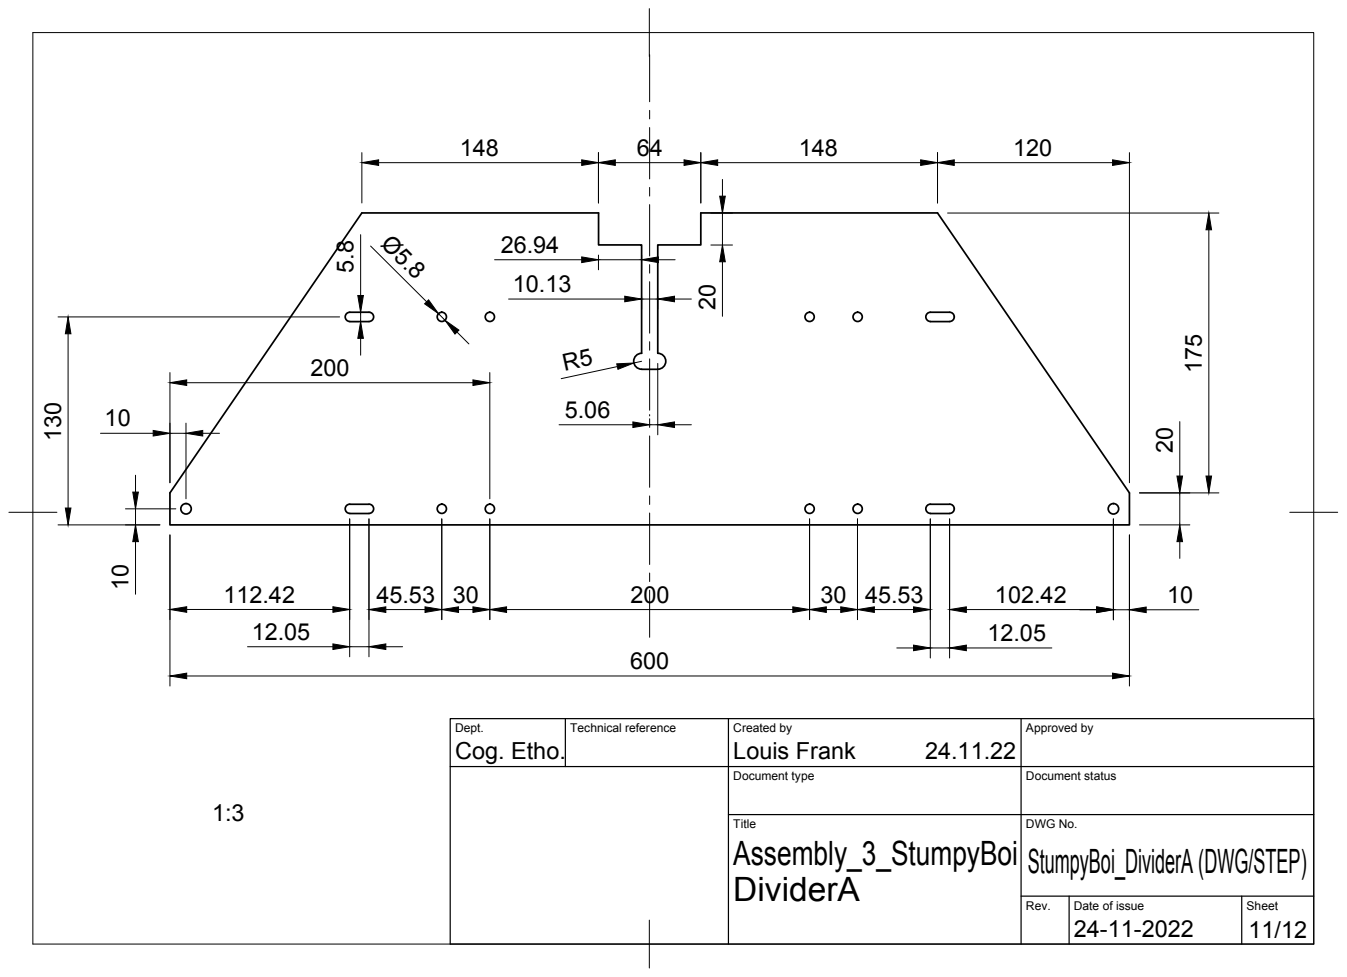
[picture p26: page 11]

Dept. Cog. Etho. | Technical reference | Created by Louis Frank 24.11.22 | Approved by

Document type | Document status

Title Assembly_3_StumpyBoi DividerA | DWG No. StumpyBoi_DividerA (DWG/STEP)

Rev. | Date of issue 24-11-2022 | Sheet

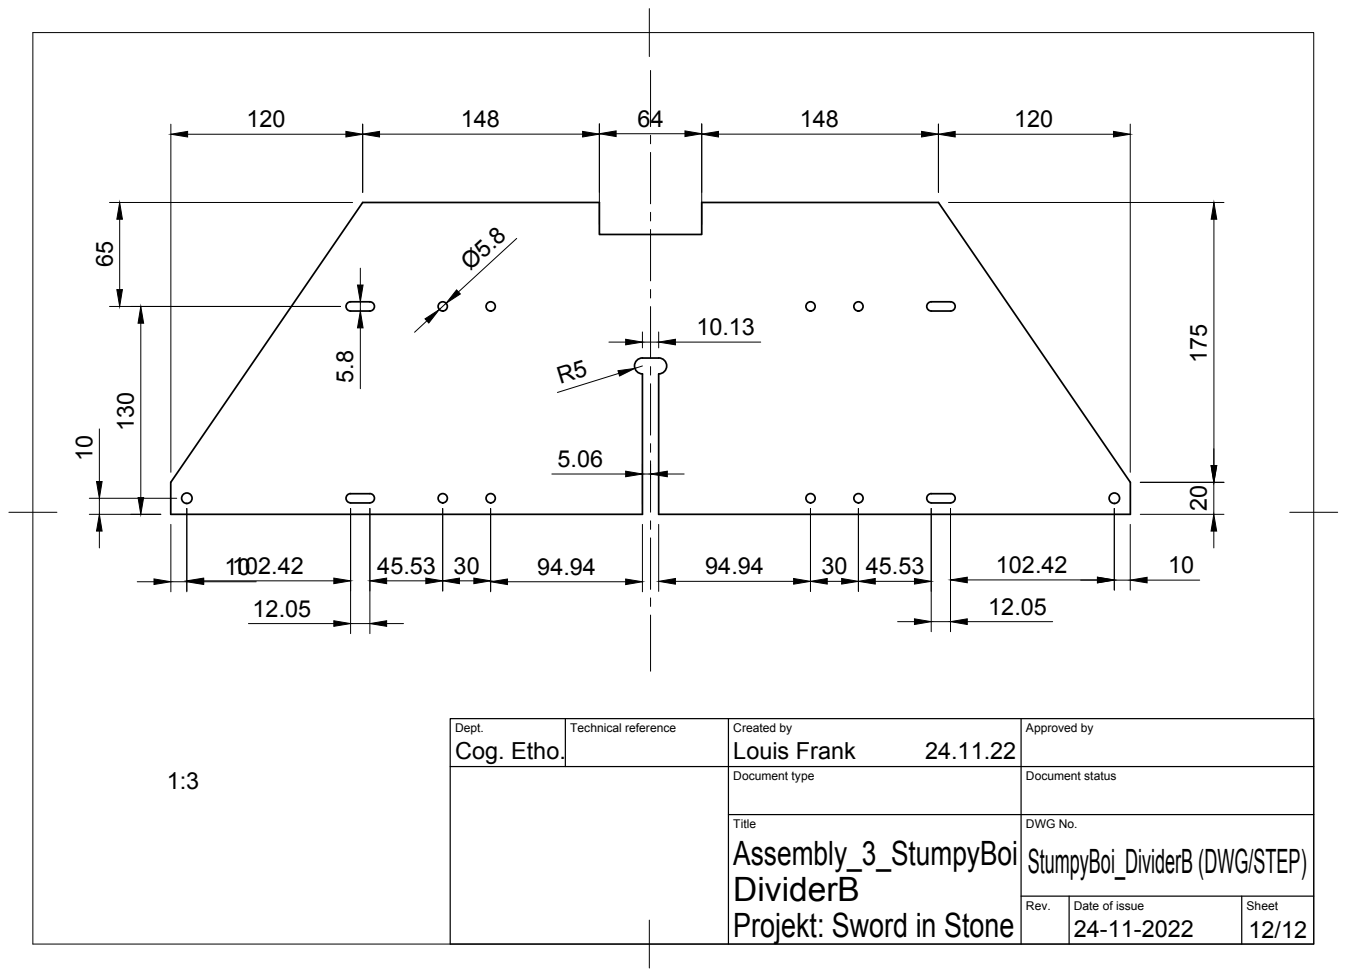
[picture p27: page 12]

Dept. Cog. Etho. | Technical reference | Created by Louis Frank 24.11.22 | Approved by

Document type | Document status

Title Assembly_3_StumpyBoi DividerB | DWG No. StumpyBoi_DividerB (DWG/STEP)

Rev. | Date of issue | Sheet

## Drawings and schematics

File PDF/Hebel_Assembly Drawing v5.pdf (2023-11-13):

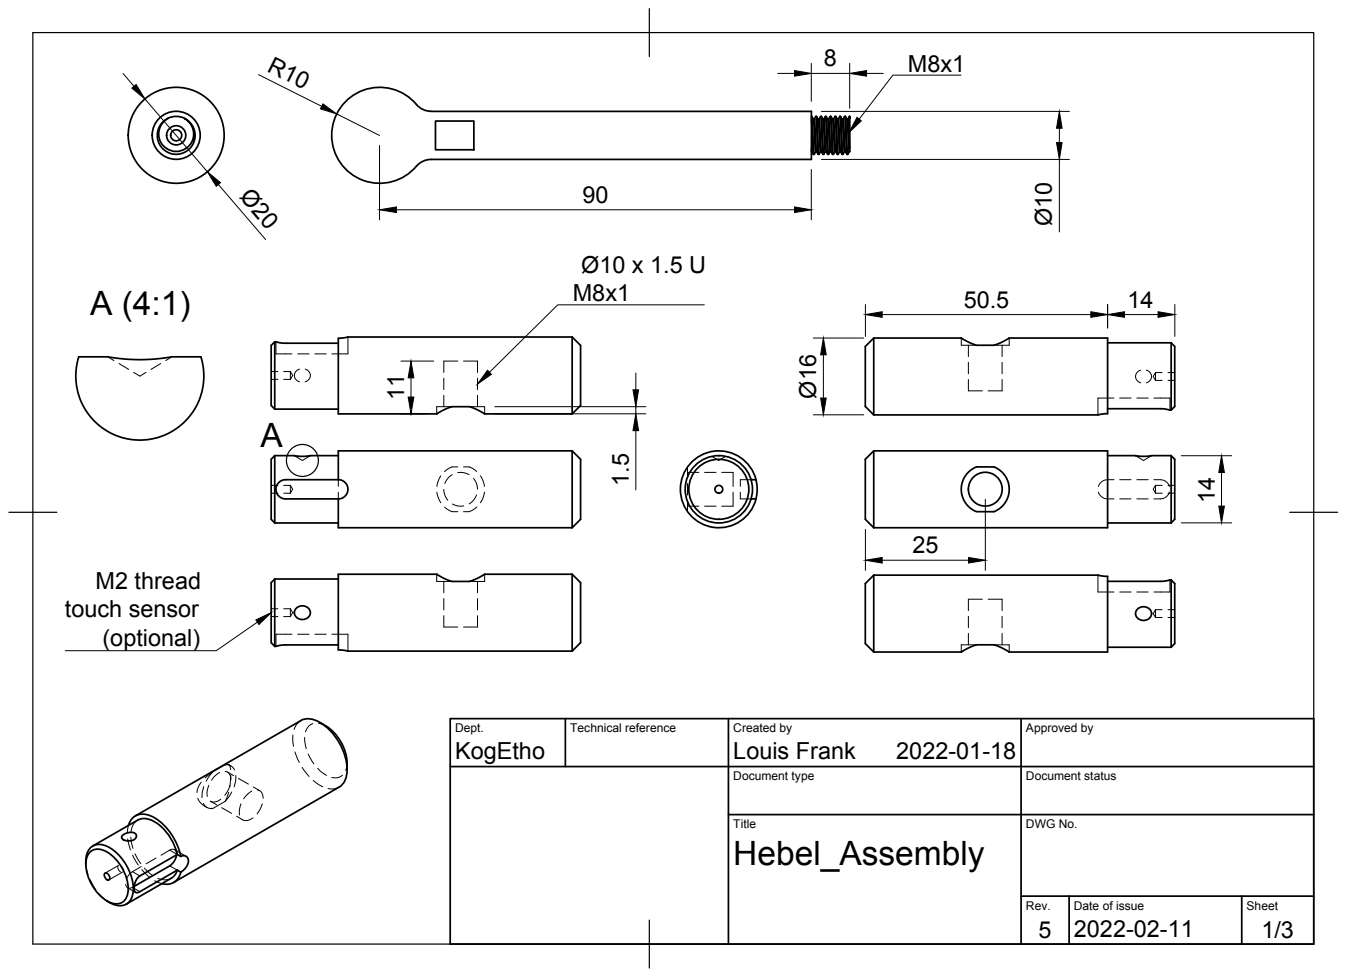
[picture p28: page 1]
M2 thread touch sensor

Dept. KogEtho | Technical reference | Created by Louis Frank 2022-01-18 | Approved by

Document type | Document status

Title Hebel_Assembly | DWG No.

Rev. 5 | Date of issue 2022-02-11 | Sheet

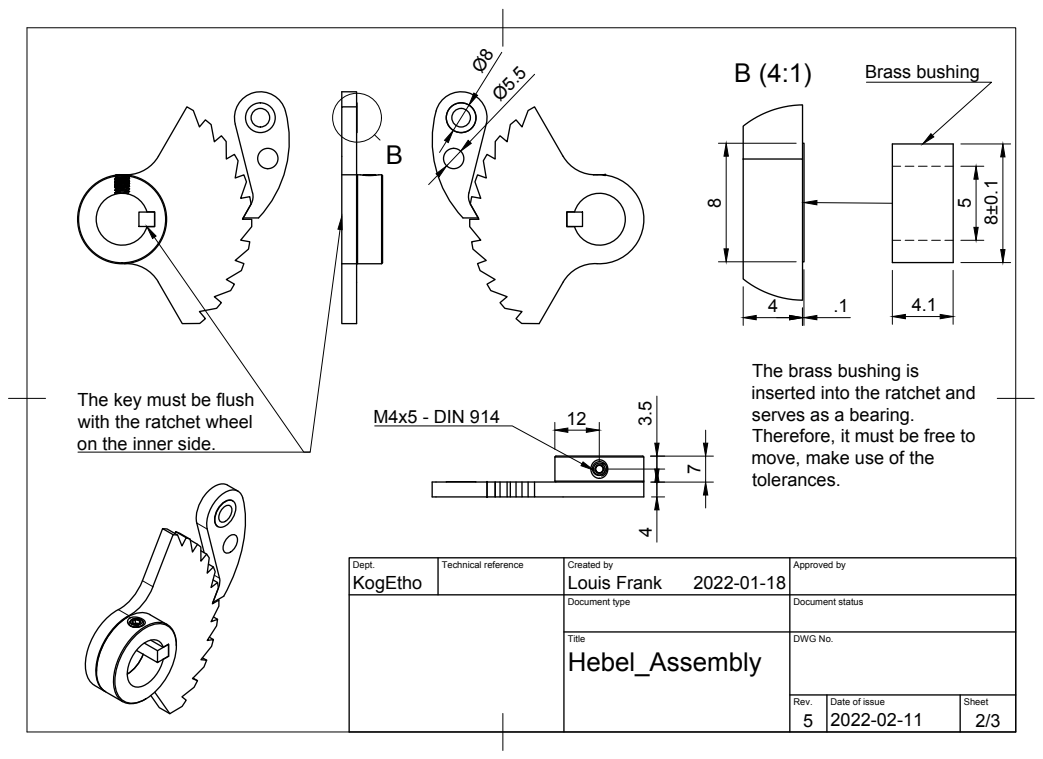
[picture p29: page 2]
Ø8 B (4:1) Brass bushing Ø5.5; M4x5 - DIN 914

The brass bushing is
inserted into the ratchet and
serves as a bearing.
Therefore, it must be free to
move, make use of the
tolerances.

7 3.5The key must be flush
with the ratchet wheel
on the inner side.

Dept. KogEtho | Technical reference | Created by Louis Frank 2022-01-18 | Approved by

Document type | Document status

Title Hebel_Assembly | DWG No.

Rev. | Date of issue | Sheet

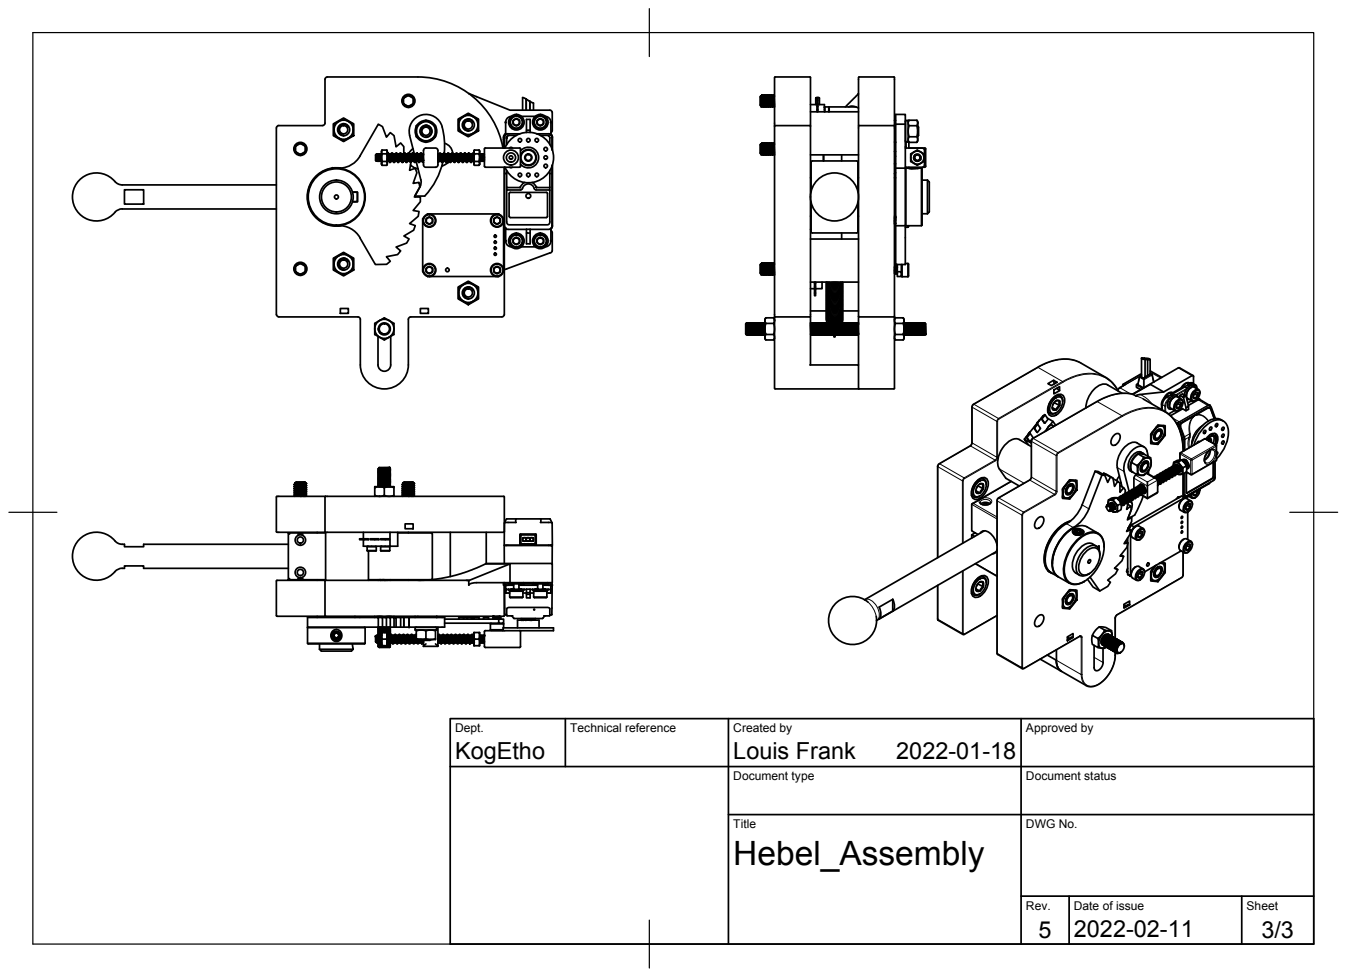
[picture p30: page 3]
Dept.; Technical reference; Created by; Approved by; Document type; Document status; Title; DWG No.; Rev.; Date of issue; Sheet; KogEtho; Louis Frank
